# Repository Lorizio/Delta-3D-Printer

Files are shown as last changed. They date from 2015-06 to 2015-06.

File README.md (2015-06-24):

# Delta 3D Printer

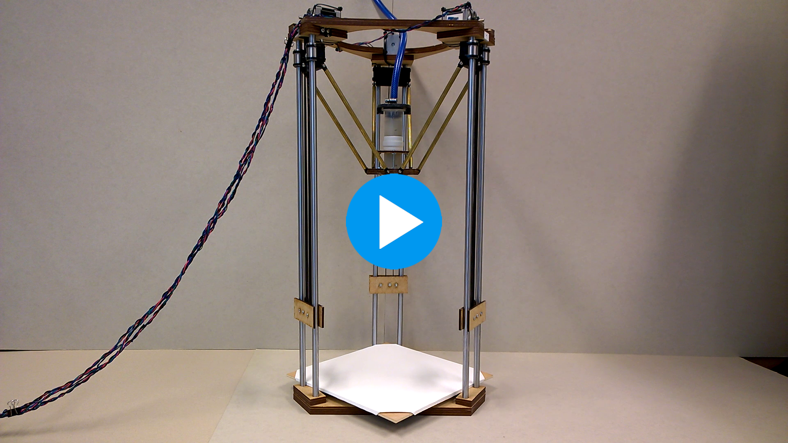
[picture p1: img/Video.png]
IMAGE ALT TEXT (https://vimeo.com/131369209)


## Project description
Model the world in a thousands possible ways, being the architect of your environment, those are the ideas of 3D printing. The recent buzz for this type of modern printing created a real phenomenon supported by countless enthusiasts, with a constant growing community trying to improve and share their knowledge about this new innovating mean of creation.
This project is one of the many that participates to the elaborated questioning of 3D printing. It investigates the art power of such a complex machinery and confirms the renaissance of third millennium craftsmen. This project gives the hints for building a homemade Delta Printer. Using clay and a common air compressor it is possible to design complex shapes effortless. 

This printer is powered by a single Arduino board and a manually controlled air compressor to extrude the printing material. Three axis on which are sliding three mounters support the extruder at the center. There is one motor per axis, positioned at the top. This printer makes use of three endstops to calibrate itself before every printing. They are positioned at the top of each axis under the motors.

[Jonathan Keep's work](http://www.keep-art.co.uk/index.htm) was a very good support and I thank him a lot for his guidelines, especially about electronic topic.

## Repository content
There are three main topics :
* [**Building**](https://github.com/Lorizio/Delta-3D-Printer/tree/master/building).
Building a delta 3D printer from scratch, create the necessary components, connect the electronics together and the power connection configuration.
* [**Software**](https://github.com/Lorizio/Delta-3D-Printer/tree/master/software).
The drivers, the communication tools between the computer and the printer, the firmware, the required softwares, the slicing of objects and the settings of the printer.
* [**Printing Material**](https://github.com/Lorizio/Delta-3D-Printer/tree/master/printing_material).
Some requirements and guidelines about printing with clay.

 A list of the required components with a corresponding URL for easy internet finding is available for a total price of less than 300$ (see __what-you-need.odt__).
 
### Process
 
 The whole process is the following :
 
 1. Build the printer 
 2. Connect the electronics
 3. Set up the firmware
 4. Set up the printer settings
 5. Print.

 Building the printer implies dealing with soldering wires. Corresponding tools are thus needed. A laser cut machine can come in handy to facilitate the process of cutting MDF panels.
 
 The two key links of the above string are the firmware and the printer settings : 
> The firmware must be adapted to correspond to the printer dimensions such as the length of the arms and the possible angle of some particular parts. This is done using Arduino (see [Software](https://github.com/Lorizio/Delta-3D-Printer/tree/master/software)). More details [here](http://www.repetier.com/firmware/v091/) and [here](http://www.repetier.com/documentation/repetier-firmware/rf-installation/). 
 > The printer settings must match the capacity of the printer (speed and size among others). 
 
_If the printer you are dealing with is essentially the same as the one in here (i.e. was made using the provided list) you shouldn't have to configure anything._

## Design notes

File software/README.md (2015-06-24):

# Software

## Driver and important steps
Connect the Arduino board to your computer. Running Windows, it should finish install itself after 2 minutes without you needing to do anything in particular (make sure you are connected to Internet so that Windows Update can download the driver). 
_If Windows is displaying any error when connecting the board you will need to manually install the driver. Check the Arduino website for more informations._

For later use **you need to know which COM port was the Arduino board installed on**. You can find this information checking the properties of the board in the "Devices and Printers" from the Control Panel. Write it down. For example, mine was installed using the port COM3.

## Communication
Apart from the 3D software modelling (see below), you will need two important software that you can download right now : **[Arduino](https://www.arduino.cc/en/Main/Software)** and **[Repetier Host](http://www.repetier.com/download/)**

### Firmware
In the Arduino folder provided in this repository you can find the firmware that you need to install on the board once. 

If the dimension of your printer do not match the components given in the provided list you will need to adjust some [settings](http://solidutopia.com/marlin-firmware-user-guide-basic/). Otherwise everything is already configured and you can do the following :

1. Double click __CeramicPrinter_MarlinLCD.ino__.
2. Click on "Tools" - "Board: "Arduino Mega or ..." and choose "Arduino Mega or Mega 2560"
3. Click on "Tools" - "Port" and you should see the corresponding port I mentioned before, namely COM3 in my case.
4. Click the "Upload" button.
5. When Arduino finishes the verification process and the upload process, you can close Arduino.

You won't be needing Arduino anymore unless you want to adjust some settings about the printer dimensions and endstops configuration.

### Slicing and sending
The extruder of the printer needs to follow a path in space. This path is defined by a software called a __slicer__. Repetier Host is a powerful software that integrates such a tool (Slic3r).

_We need to configure Repetier Host and Slic3r_:

First of all, open Repetier Host.

#### Repetier Host
Hit CTRL+P to open the printer settings (or click on "Configuration" in the menu and select "Printer settings"). Enter a name for your printer in the top textbox and copy the settings from the following screenshots :

__Note that the Port number might not be the same for you__
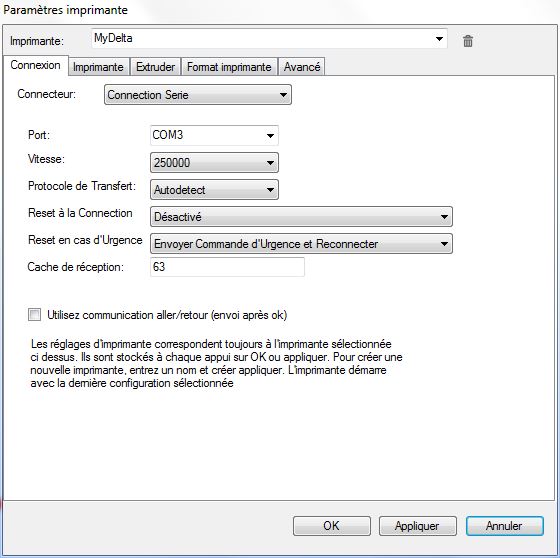
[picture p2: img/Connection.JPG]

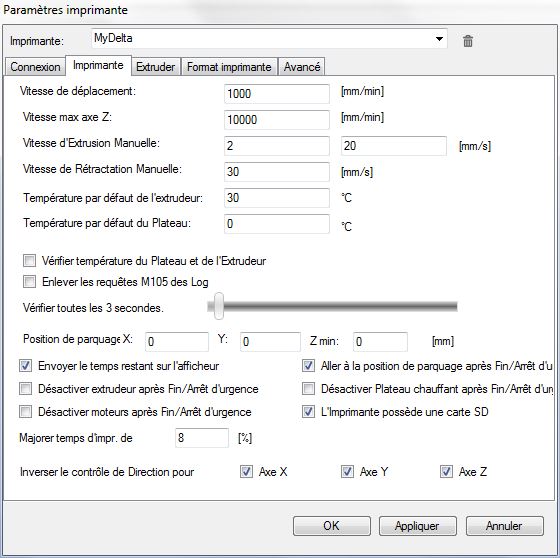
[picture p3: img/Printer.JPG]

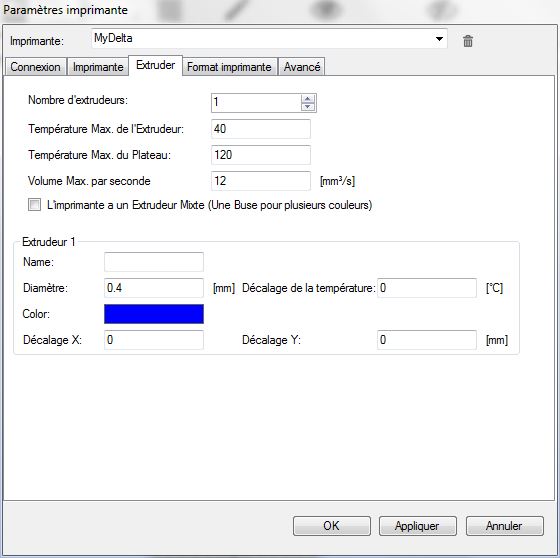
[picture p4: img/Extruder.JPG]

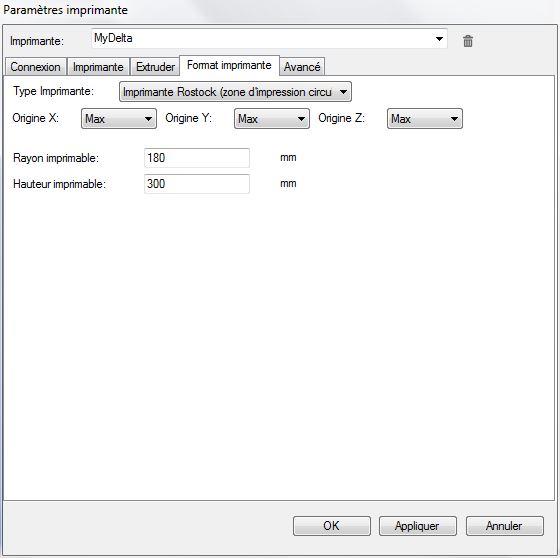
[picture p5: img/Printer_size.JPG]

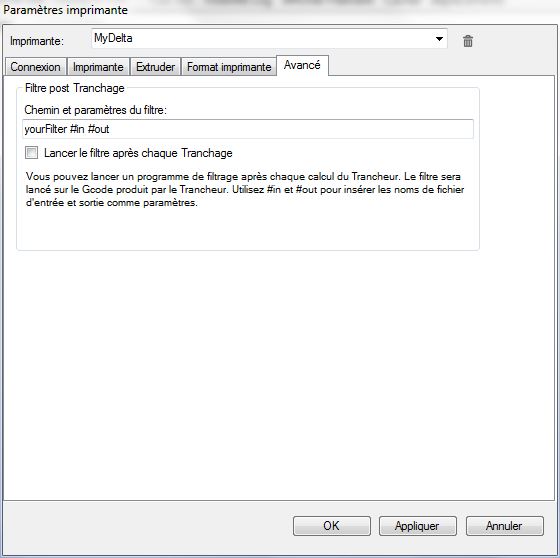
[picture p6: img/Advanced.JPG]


Click OK to apply settings.

#### Slic3r
1. From the main Repetier Host click the "Slicer" tab on the right. 
2. Select "Slic3r" from the "Slicer" drop menu and hit the "Configuration" button.
3. In the new opened window, click "File" from the menu and select "Load Config ..."
4. Select the **config.ini** provided in this repository in the Slic3r folder.

**_Note : Slic3r won't permanently save the new config unless you hit the "Save" icon in every section._**

You can close the Slic3r window.

### It's alive
Your printer should be ready to use if you followed all the steps mentioned above. Close Arduino and Repetier Host, disconnect the board from your computer.

To make sure everything works as expected always do the following when using the printer :
1. Connect the USB cable from the Arduino board. The board should light up.
2. Connect the power cable of the board to current (you might want to use a multi-socket plug with an ON/OFF button).
3. Launch Repetier Host.
4. Use the button "Connect" in the top left corner to connect to the printer. It should turn green when successfully connected.

You are now ready to test the printer behaviour.
Prepare your extruder and connect it the pipe of the air compressor. Leave it closed and install it in the printer to simulate a real printing.

Proceed with the following :

0. __Connect to the printer__. In the main Repetier Host window, check that you are connected to the printer by verifying that the "Connect" button is green. If it's not, follow the latter advice.
1. __Import the object__. In the right panel, select the first tab labelled "Object Placement". Import the desired shape to print using the "+" button. You can import any STL file and make them bigger, crop them and move them as you want. 
2. __Slice it__. In the third panel labelled "Slicer", hit the big button called "Slice with Slic3r". The fourth tab should then open and display the time it will take for the printer to print the object and some other informations.
3. __Launch it__. Hit the "Play" button and watch your printer move.

**_Be ready to push the RESET button on the Arduino board in case of any unwanted behaviour due to bad settings_**

## Shapes
You should be able to print almost any kind of shapes depending on your extruder precision.

Repetier Host can import STL format of 3D modeling. You can use any 3D modeler such as [Rhinoceros](https://www.rhino3d.com/), [Grasshoper](http://www.grasshopper3d.com/) or [Blender](https://www.blender.org/) to achieve this. Don't forget to save your shapes in the STL format.

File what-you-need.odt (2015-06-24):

You will need an air compressor machine accurate enough to control the pressure efficiently.

Structure parts :

High torque hybrid (3x)

http://www.zappautomation.co.uk/sy42sth47-1684a-high-torque-hybrid-stepper-motors.html

12mm steel rods (6x)

http://www.zappautomation.co.uk/sfc12-precision-round-rail.html

12 mm linear bearing (6x)

They need to slide along the steel rods smoothly

http://www.zappautomation.co.uk/lm10uu-linear-bearing-29451.html

GT2 belts (3x)

http://www.amazon.com/3DMakerWorld-GT2-Timing-Belt/dp/B00IDCG6ZU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

Traxxas 5347 with hollows balls (12x)

They must fit in the brass tube below. Two per tube.

http://www.amazon.com/Traxxas-5347-Hollow-Balls-Large/dp/B000BOLVJY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

Brass tube 8mm (6x)

Two tubes per axis. 23 centimeters each. The material doesn’t matter as long as it is solid and that the traxxas pieces can fit inside.

http://www.amazon.com/Engineering-Round-Brass-Tube-45/dp/B005WPASOG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

xbox 360 203W power brick 220V

http://www.amazon.co.uk/OFFICIAL-MICROSOFT-REPLACEMENT-POWER-SUPPLY/dp/B00AUYDF6M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

Some MDF panels of at least 12 mm.

Electronic part

Ultra Set (1x)

It comes with wires and all the required electronic components

https://gadgets3d.eu/index.php?route=product/product&product_id=70

Extruder parts

Glue Liquid Cartridge Dispenser Syringe Barrel 300CC Clear Black

http://www.amazon.co.uk/Liquid-Cartridge-Dispenser-Syringe-Barrel/dp/B00GMW4EBG

tips

http://www.adhesivedispensers.co.uk/TE714025PK.htm

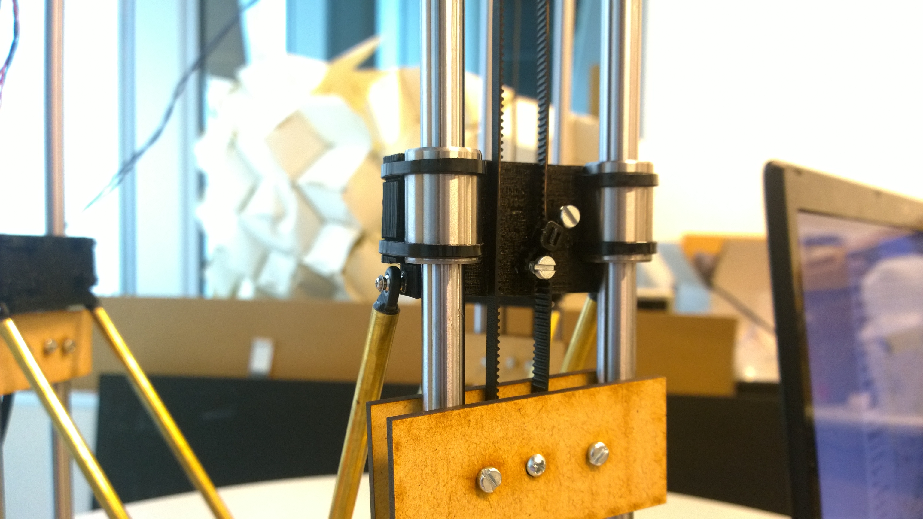
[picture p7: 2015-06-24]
img/Mounter.jpg

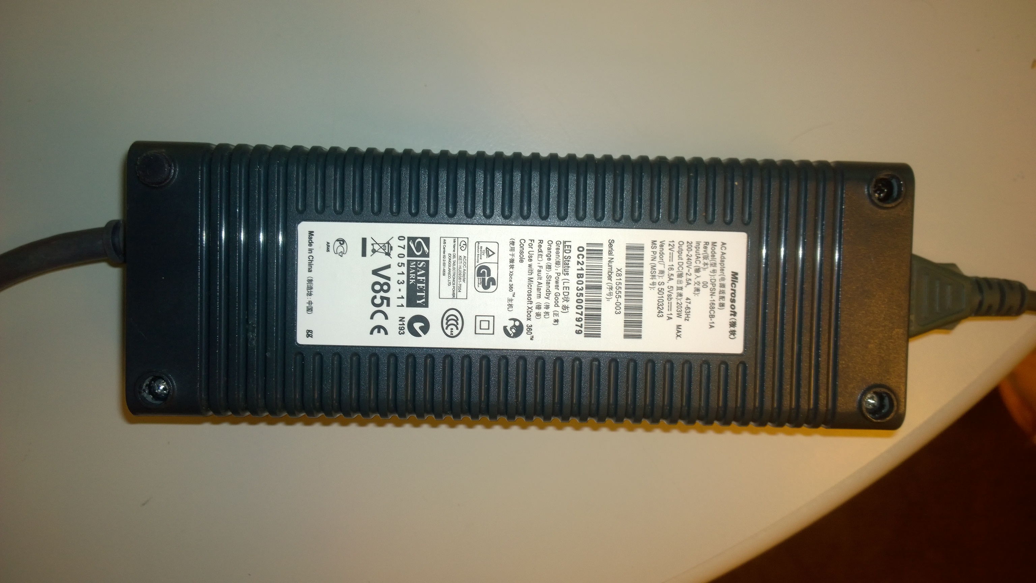
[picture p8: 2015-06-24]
img/Powerbrick.jpg

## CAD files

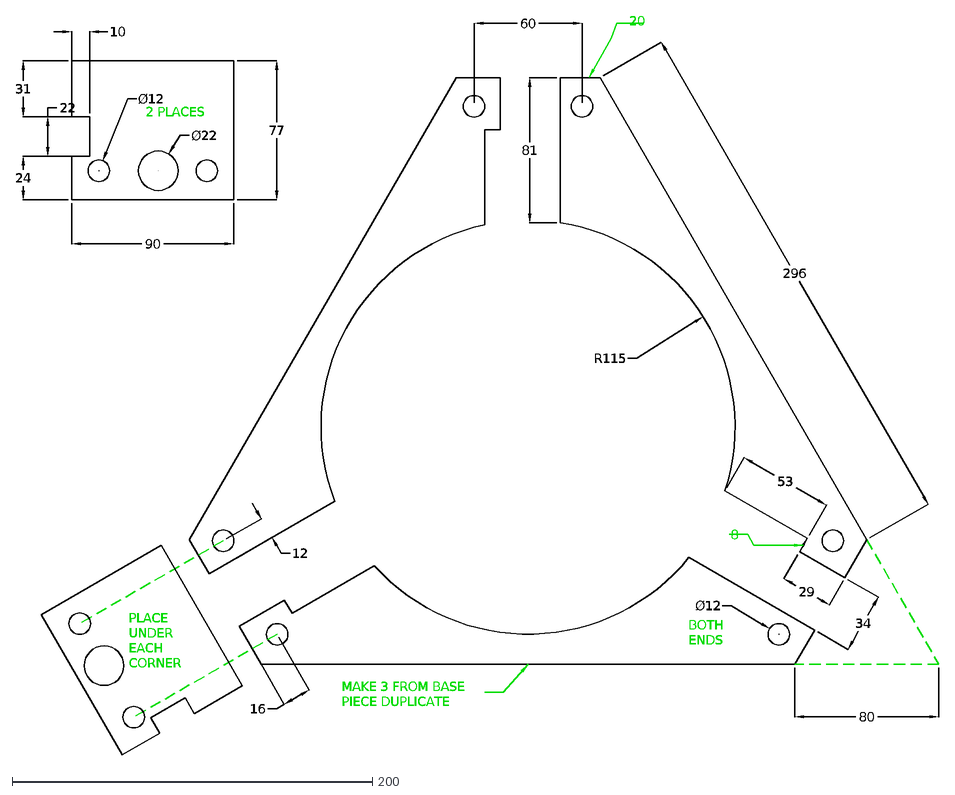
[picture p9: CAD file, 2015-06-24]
building/DXF_files/TOP_ASSEMBLY.dxf
80
34
R115
296
81
29
53
60
8
20
12
16
90
77
31
24
22
10
Ø12
2 PLACES
Ø22
BOTH
ENDS
PLACE
UNDER
EACH
CORNER
MAKE 3 FROM BASE
PIECE DUPLICATE

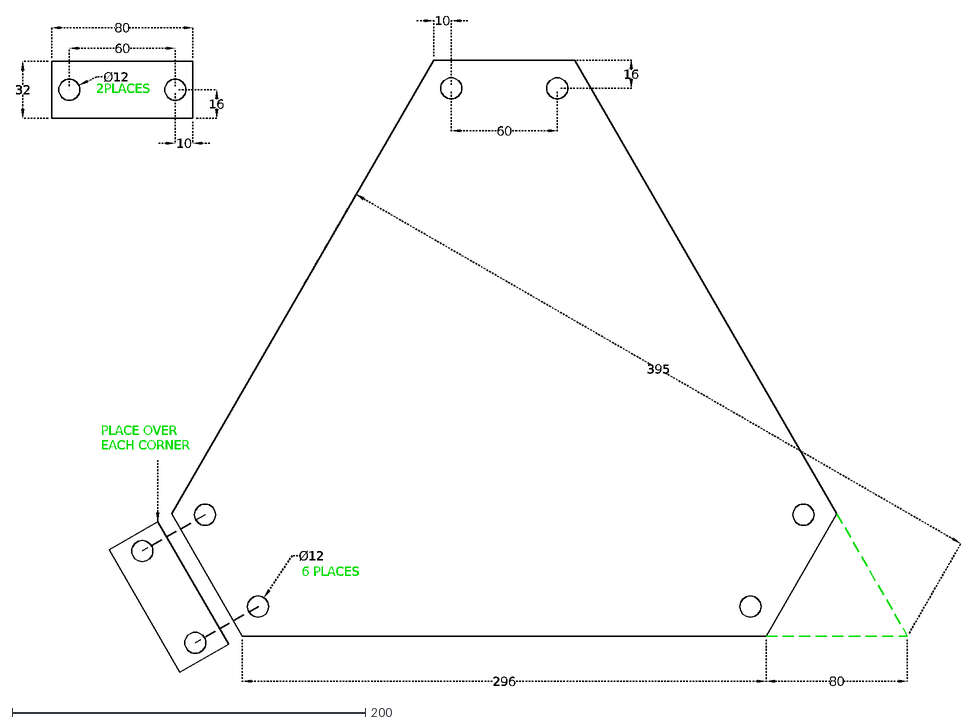
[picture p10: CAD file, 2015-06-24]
building/DXF_files/BASE.dxf
80
296
395
16
60
10
Ø12
6 PLACES
32
2PLACES
PLACE OVER
EACH CORNER

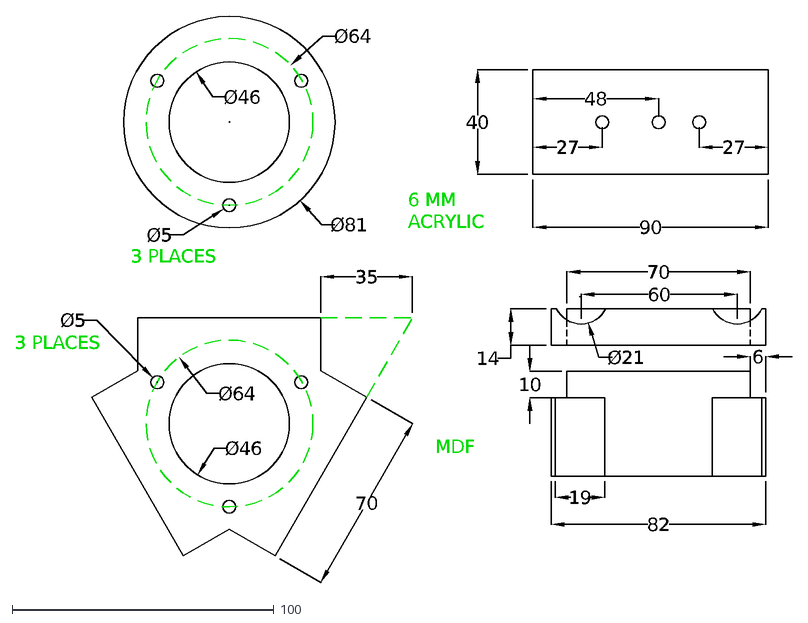
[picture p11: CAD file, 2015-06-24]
building/DXF_files/COMPONENTS.dxf
Ø46
Ø81
Ø64
Ø5
3 PLACES
70
35
Ø21
14
10
40
90
27
48
6 MM
ACRYLIC
MDF
60
82
19
6

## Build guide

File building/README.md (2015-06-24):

# Instructions

## Structure
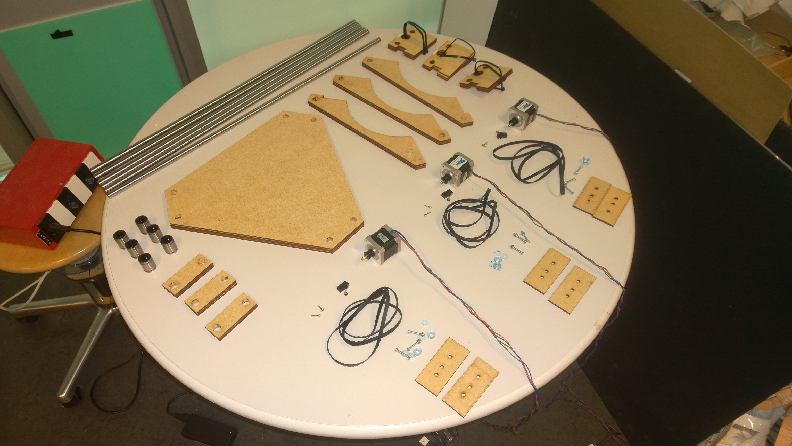
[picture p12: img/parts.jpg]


You can find the DXF files as blueprints in the DXF_files folder (credits to John Nicholson). They are very useful, specially if you can benefit the use of a laser cut machine. Use them to cut the MDF panels.

Watch Jonathan Keep's [video](https://www.youtube.com/watch?v=MYd_AmkCWfM) to have an idea of how to assemble every parts together.

## Electronics

### Endstops
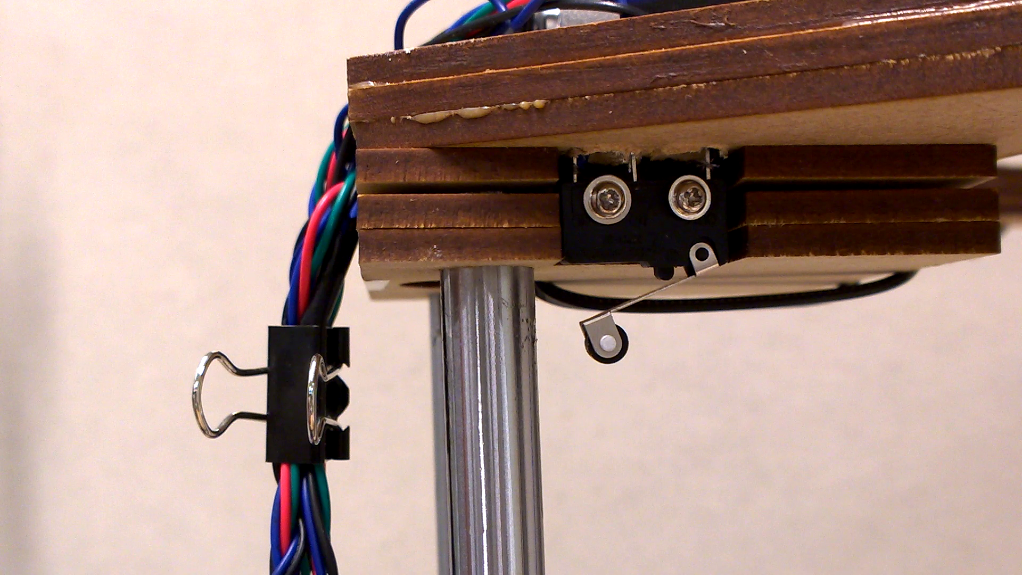
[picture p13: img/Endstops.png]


Take the wires from the Ultra Set labeled "ENDSTOP". You can cut the red ones out. For each endstop, connect the blue wire to the endstop tip labeled normally closed (NC), and connect the black wire to the endstop tip labeled (COM).

### Motors
Take the wires from the Ultra Set labeled "MOTOR" and solder each wire with each matching color wire of the step motor.

On the Arduino Board you need to configure the motor component. Jonathan Keep gives the following advice :

> Stepper motor tuning : Each stepper motor driver board has two star headed adjustment screws. [...] I have found turning the flat side [clockwise] to around three o’clock is strong enough without the motors getting too hot during continues printing. I am not quite sure what the lower screw is for but on the fabster3D EBay webpage they suggest leaving them turned fully anticlockwise. 

### Thermostat
The Ultra Set supply a very small and thin thermostat. Take the wires labeled "THERM" and solder them to the thermostat. This is necessary as the Ultra Set was thought to work with hot material and has mandatory security check systems. 

### Arduino board connections
Take the following from the Ultra Set :

- LCD screen
- SD Card
- The "L" shaped small board
- Arduino board
- The two large cables for connecting the LCD screen

When facing the Arduino board, you should see the power socket in the bottom left corner. Connect the wires from the motors, the wires from the endstops and the L shaped board as the following :

(photos credits to Jonathan Keep)

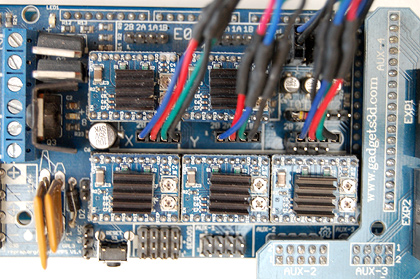
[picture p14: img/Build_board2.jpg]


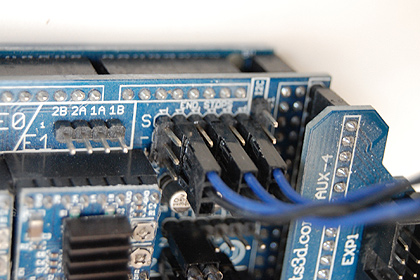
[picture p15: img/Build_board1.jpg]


Connect the thermostat in the T0 location, just under the endstops pin.
Finally connect the two large cables between the LCD screen and the L shaped board, and put the SD card in behind the LCD screen.

### Power supply
Cut the end of the XBOX power brick and connect the wires as the following :

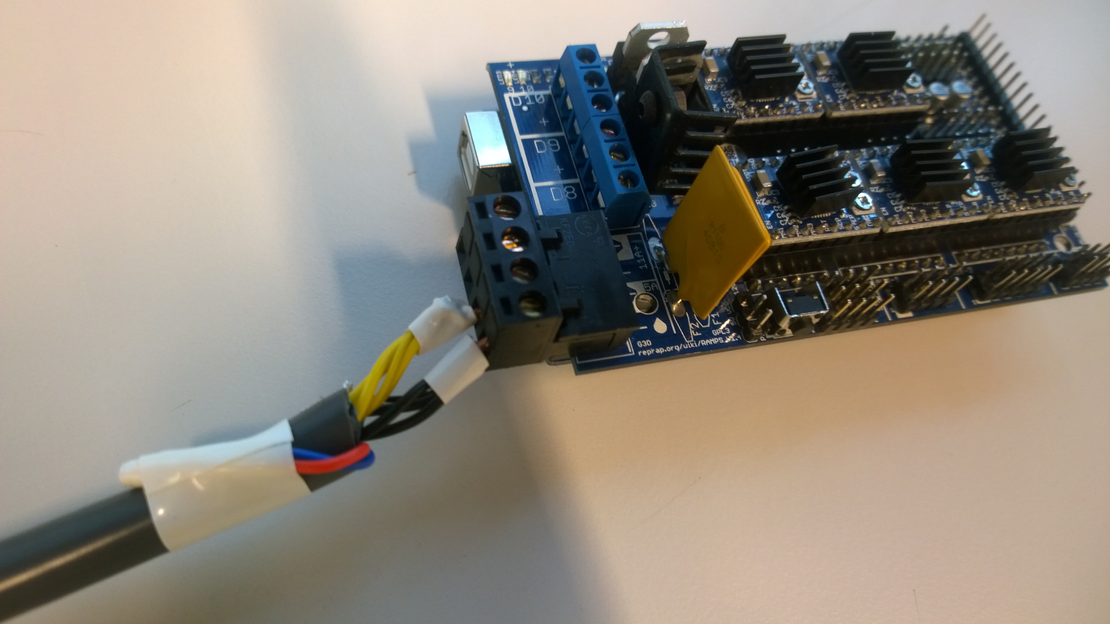
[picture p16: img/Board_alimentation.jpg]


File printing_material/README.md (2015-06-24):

# Printing Material

Using any kind of clay from any DIY store, you can obtain some very nice results by mixing it with a small amount of water. I personally add 0.05 liter of water for 300gr of clay and an air pressure of about 1 bar. You need to find the perfect balance in the mixing recipe and the corresponding air pressure needed to achieve the best of the 3D printing. 

A too wet mixing will collapse under its own weight while a too dry mixing might induce issues with the air compressor and the water tightness of the extruder.

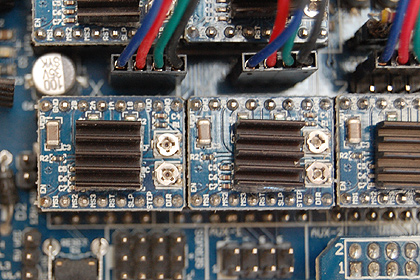
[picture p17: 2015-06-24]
img/Build_stepper.jpg

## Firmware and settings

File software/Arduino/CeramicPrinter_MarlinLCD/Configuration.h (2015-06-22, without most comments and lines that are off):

#define CONFIGURATION_H
#define STRING_VERSION_CONFIG_H __DATE__ " " __TIME__ // build date and time
#define STRING_CONFIG_H_AUTHOR "(jcrocholl, deltabot)" //Who made the changes.
#define SERIAL_PORT 0
#define BAUDRATE 250000
#define MOTHERBOARD 33
#define DELTA_SEGMENTS_PER_SECOND 100
#define DELTA_DIAGONAL_ROD 240.0 // mm
#define DELTA_SMOOTH_ROD_OFFSET 192.0 // mm
#define DELTA_EFFECTOR_OFFSET 8.0 // mm
#define DELTA_CARRIAGE_OFFSET 50.0 // mm
#define DELTA_RADIUS (DELTA_SMOOTH_ROD_OFFSET-DELTA_EFFECTOR_OFFSET-DELTA_CARRIAGE_OFFSET)
#define SIN_60 0.8660254037844386
#define COS_60 0.5
#define DELTA_TOWER1_X -SIN_60*DELTA_RADIUS // front left tower
#define DELTA_TOWER1_Y -COS_60*DELTA_RADIUS
#define DELTA_TOWER2_X SIN_60*DELTA_RADIUS // front right tower
#define DELTA_TOWER2_Y -COS_60*DELTA_RADIUS
#define DELTA_TOWER3_X 0.5 // back middle tower
#define DELTA_TOWER3_Y DELTA_RADIUS
#define TEMP_SENSOR_0 2
#define TEMP_SENSOR_1 0
#define TEMP_SENSOR_2 0
#define TEMP_SENSOR_BED 0
#define TEMP_RESIDENCY_TIME 2	// (seconds)
#define TEMP_HYSTERESIS 30       // (degC) range of +/- temperatures considered "close" to the target one
#define TEMP_WINDOW     1       // (degC) Window around target to start the recidency timer x degC early.
#define HEATER_0_MINTEMP 5
#define HEATER_1_MINTEMP 5
#define HEATER_2_MINTEMP 5
#define BED_MINTEMP 5
#define HEATER_0_MAXTEMP 275
#define HEATER_1_MAXTEMP 275
#define HEATER_2_MAXTEMP 275
#define BED_MAXTEMP 150
#define PIDTEMP
#define PID_MAX 255 // limits current to nozzle; 255=full current
  #define PID_FUNCTIONAL_RANGE 10 // If the temperature difference between the target temperature and the actual temperature
  #define PID_INTEGRAL_DRIVE_MAX 255  //limit for the integral term
  #define K1 0.95 //smoothing factor withing the PID
  #define PID_dT ((16.0 * 8.0)/(F_CPU / 64.0 / 256.0)) //sampling period of the temperature routine
    #define  DEFAULT_Kp 22.2
    #define  DEFAULT_Ki 1.08
    #define  DEFAULT_Kd 114
#define MAX_BED_POWER 255 // limits duty cycle to bed; 255=full current
#define PREVENT_DANGEROUS_EXTRUDE
#define PREVENT_LENGTHY_EXTRUDE
#define EXTRUDE_MINTEMP 170
#define EXTRUDE_MAXLENGTH (X_MAX_LENGTH+Y_MAX_LENGTH) //prevent extrusion of very large distances.
  #define ENDSTOPPULLUP_XMAX
  #define ENDSTOPPULLUP_YMAX
  #define ENDSTOPPULLUP_ZMAX
  #define ENDSTOPPULLUP_XMIN
  #define ENDSTOPPULLUP_YMIN
  #define ENDSTOPPULLUP_ZMIN
const bool X_ENDSTOPS_INVERTING = false; // set to true to invert the logic of the endstops.
const bool Y_ENDSTOPS_INVERTING = false; // set to true to invert the logic of the endstops.
const bool Z_ENDSTOPS_INVERTING = false; // set to true to invert the logic of the endstops.
#define X_ENABLE_ON 0
#define Y_ENABLE_ON 0
#define Z_ENABLE_ON 0
#define E_ENABLE_ON 0 // For all extruders
#define DISABLE_X false
#define DISABLE_Y false
#define DISABLE_Z false
#define DISABLE_E false // For all extruders
#define INVERT_X_DIR false    // for Mendel set to false, for Orca set to true
#define INVERT_Y_DIR false    // for Mendel set to true, for Orca set to false
#define INVERT_Z_DIR false    // for Mendel set to false, for Orca set to true
#define INVERT_E0_DIR false   // for direct drive extruder v9 set to true, for geared extruder set to false
#define INVERT_E1_DIR false   // for direct drive extruder v9 set to true, for geared extruder set to false
#define INVERT_E2_DIR false   // for direct drive extruder v9 set to true, for geared extruder set to false
#define X_HOME_DIR 1
#define Y_HOME_DIR 1
#define Z_HOME_DIR 1
#define min_software_endstops true //If true, axis won't move to coordinates less than *_MIN_POS.
#define max_software_endstops true //If true, axis won't move to coordinates greater than *_MAX_POS.
#define X_MAX_POS 90
#define X_MIN_POS -90
#define Y_MAX_POS 90
#define Y_MIN_POS -90
#define Z_MAX_POS MANUAL_Z_HOME_POS
#define Z_MIN_POS 0
#define X_MAX_LENGTH (X_MAX_POS - X_MIN_POS)
#define Y_MAX_LENGTH (Y_MAX_POS - Y_MIN_POS)
#define Z_MAX_LENGTH (Z_MAX_POS - Z_MIN_POS)
#define MANUAL_HOME_POSITIONS  // If defined, MANUAL_*_HOME_POS below will be used
#define MANUAL_X_HOME_POS 0
#define MANUAL_Y_HOME_POS 0
#define MANUAL_Z_HOME_POS 320  // In mm, was 350 - Distance between nozzle and print surface after homing.
#define NUM_AXIS 4 // The axis order in all axis related arrays is X, Y, Z, E
#define HOMING_FEEDRATE {1200, 1200, 1200, 0}  // set the homing speeds (mm/min)
#define Z_PROBE_OFFSET {0, 13.6, 6.6, 0}  // Distance between hotend nozzle and deployed bed leveling probe.
#define DEFAULT_AXIS_STEPS_PER_UNIT   {80, 80, 80, 100}
#define DEFAULT_MAX_FEEDRATE          {500, 500, 500, 25}  // (mm/sec)originaly {320,320,320,25}
#define DEFAULT_MAX_ACCELERATION      {2000, 2000, 2000, 2000}    // X, Y, Z, E maximum start speed for accelerated moves.
#define DEFAULT_ACCELERATION          2000   // X, Y, Z and E max acceleration in mm/s^2 for printing moves
#define DEFAULT_RETRACT_ACCELERATION  2000   // X, Y, Z and E max acceleration in mm/s^2 for r retracts
#define DEFAULT_XYJERK                20.0   // (mm/sec)
#define DEFAULT_ZJERK                 20.0   // (mm/sec)
#define DEFAULT_EJERK                 20.0   // (mm/sec)
#define ULTIMAKERCONTROLLER //as available from the ultimaker online store.
 #define ULTIPANEL
 #define NEWPANEL
#define PLA_PREHEAT_HOTEND_TEMP 180
#define PLA_PREHEAT_HPB_TEMP 70
#define PLA_PREHEAT_FAN_SPEED 255		// Insert Value between 0 and 255
#define ABS_PREHEAT_HOTEND_TEMP 240
#define ABS_PREHEAT_HPB_TEMP 100
#define ABS_PREHEAT_FAN_SPEED 255		// Insert Value between 0 and 255
  #define NEWPANEL  //enable this if you have a click-encoder panel
  #define SDSUPPORT
  #define ULTRA_LCD
  #define LCD_WIDTH 20
  #define LCD_HEIGHT 4
#include "Configuration_adv.h"
#include "thermistortables.h"

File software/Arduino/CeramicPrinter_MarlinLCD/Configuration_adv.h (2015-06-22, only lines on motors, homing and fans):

#define ENDSTOPS_ONLY_FOR_HOMING // If defined the endstops will only be used for homing
  #define X_HOME_POS MANUAL_X_HOME_POS
  #define Y_HOME_POS MANUAL_Y_HOME_POS
  #define Z_HOME_POS MANUAL_Z_HOME_POS
#define X_HOME_RETRACT_MM 1 //was 5
#define Y_HOME_RETRACT_MM 1
#define Z_HOME_RETRACT_MM 1
#define QUICK_HOME  //if this is defined, if both x and y are to be homed, a diagonal move will be performed initially.
#define MICROSTEP1 LOW,LOW
#define MICROSTEP2 HIGH,LOW
#define MICROSTEP4 LOW,HIGH
#define MICROSTEP8 HIGH,HIGH
#define MICROSTEP16 HIGH,HIGH
#define MICROSTEP_MODES {16,16,16,16,16} // [1,2,4,8,16]
#define DIGIPOT_MOTOR_CURRENT {135,135,135,135,135} // Values 0-255 (RAMBO 135 = ~0.75A, 185 = ~1A)
